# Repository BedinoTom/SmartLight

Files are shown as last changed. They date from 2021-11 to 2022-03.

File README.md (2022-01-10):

# SmartLight
Un boitier permettant de réguler l'éclairage publique, plus un dirigeable assurant la redondance du système.
## Cahier des charges
Le cahier des charges du projet : [Link](CdC.pdf)
## Rapport de séances
Un lien vers les rapports de séance : [Link](RapportSeance/Tom)
## Boitiers
Ce dossier contient tout le travail liée au boitier : [Link](Boitiers/README.md)
## Dirigeable
Ce dossier contient tout le travail lié au Dirigeable : [Link](Dirigeable/README.md)
## Images
Ce dossier contient toutes les images du projet : [Link](Images)
## Presentations
Ce dossier contient les divers présentations du projet : [Link](Presentations/README.md)

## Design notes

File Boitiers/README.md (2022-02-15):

# Boitier
Cette partie du git est réservé aux documents de développement du boitier.

## Programme
Voici la liste des progammes conçu pour le dirigeable:
- [Main](main_firmware) : Programme principale du projet.
- [Capteur Doppler](doppler_test) : Programme permettant de détecter un mouvement par effet Doppler.
- [Capteur Photodiode](lumen_test) : Programme permettant de lire le signal analogique 
représentant la quantité de lumière.
- [Timer](timer_test) : Programme permettant de sauvegarder et de lire la date.
- [Camera Thermique](temperatureMatrix) : Programme permettant de récuperer la matrice thermique.
- [Module bluetooth](ble_test) : Programme permettant de tester le bluetooth.
- [SmartApp](SmartLightApp) : Application Android.
- [c_lib](c_lib) : Fonctionnalitées pour décoder.
- [Bluetooth decode](ble_decode) : Programme de décodage des commandes de l'application

## Modèle 3D
Voici la liste des modèles 3D liée au boitier :
- [Plaquette](schema_impression_3d) : Modèle de la plaquette tenant les capteurs afin de les tester
en condition stable.

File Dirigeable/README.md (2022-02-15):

# Dirigeable
Cette partie du git est réservé aux documents de développement du dirigeable.

## Maixduino
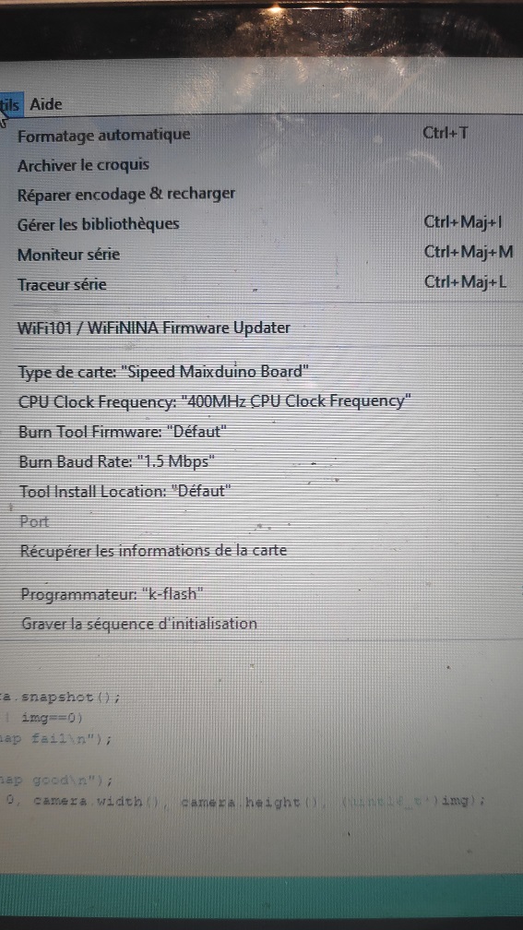
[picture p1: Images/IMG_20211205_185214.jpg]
Configuration
Voici une photo montrant la configuration IDE Arduino : 
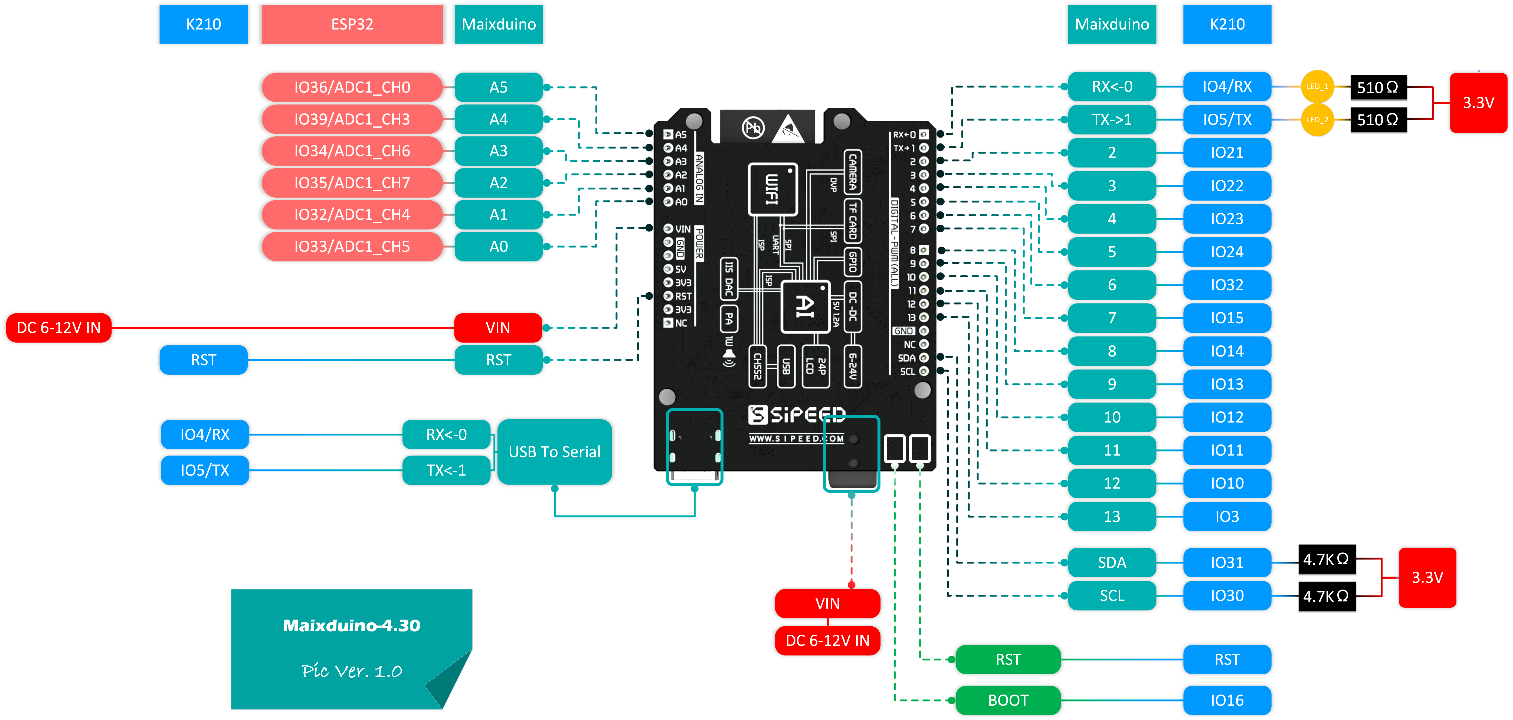
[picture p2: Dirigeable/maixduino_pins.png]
Pins Configuration
Voici la configuration des pins : 

## Programme
Voici la liste des progammes conçu pour le dirigeable:
- [Selfie](programme/selfie) : Programme permettant d'afficher le flux video de la camera sur l'écran.
- [main_firmware](programme/main_firmware) : Programme permettant d'effectuer la reconnaisse IA depuis la camera.
(Nécessite le modelè [m.kmodel](mobilenet_model/m.kmodel), il doit etre renomer en "m" et mis sur une SD) (OBSOLETE)
- [yolo_firmware](programme/yolo_firmware) : Programme permettant d'effectuer la reconnaisse IA depuis la camera.
(Le modèle [YOLO](yolo2_model/) est directement intégré dans le micrologiciel)
- [Controle_du_drone](controle_drone_firmware) : Programme pour controller les moteurs du drones.
- [arduino_i2c_slave](arduino_i2c_slave) : Programme I2C esclave.
- [ble_decode](ble_decode) : Programme de décodage des commandes bluetooth.
- [i2c_com](i2c_com) : Programme de la Maixduino pour communication "binaire".

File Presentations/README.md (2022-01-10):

# Présentations
Le projet d'Arduino qui nous a été confié cette année, nécéssite deux présentations. Une a mis parcours
et une à la fin. Elles sont toutes les deux présentes ici.

## Semestre 3
Voici celle réalisée lors du semestre 3 : [Link](S3)

## Semestre 4
Voici celle réalisée lors du semestre 4 : [Link](S4)

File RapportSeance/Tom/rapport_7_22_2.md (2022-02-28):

# Rapport de séance 7 du 22/02

Lors de cette séance, j'ai procédé au montage final du boitier avec tous les capteurs et composants nécéssaire. J'ai également utilisé
le travail éffectué à la maison afin de décoder les commandes envoyers par l'application. Pour finir j'ai recu le matériel afin
d'effectuer la liaison entre lampadaire.

## Travail éffectué à la maison

### Boitier

Juste avant le départ en vacance, j'ai déssiné puis imprimer un boiter en bois afin de contenir l'ensemble du système au sol.
Ce dernier a également 2 percages afin de laisser le champ de la caméra thermique libre et pour que la lumiere rentre et soit captée
par la capteur de luminosité. (On pourra la voir dans les images des sections suivantes)

### Communication Maixduino et Arduino

Lors des vacances j'ai finalisé la communication entre la Maixduino et l'Arduino, celle ci s'effectue par cable comme décrit dans 
le rapport précédent. La liaison est à présent pleinenement opérationnel.

### Réparation de la librairie

Les divers fonctions permettant de décoder les commandes aux format key=value; sont remplacés par une seul fonction, qui prend
en entrée le chaine brut, et la clé désirée et renvoie la valeur. La fonction a été réécrite avec des standards d'Arduino afin
qu'elle ne présente plus de bugs.

## Montage Final

Le but principal de la séance était de monter tous les capteurs ensembles et de faire fonctionner le programme principal. Il a donc
fallu monter tous les capteurs sur 2 board par soucis d'accécibilité. Et il a fallu fusionner tous les programmes qui ont été testé.
Comme on peut le voir sur l'image, la plaquette qui supporte le doppler et la caméra thermique a été collés dans la boitier par soucis
de simpliciter.
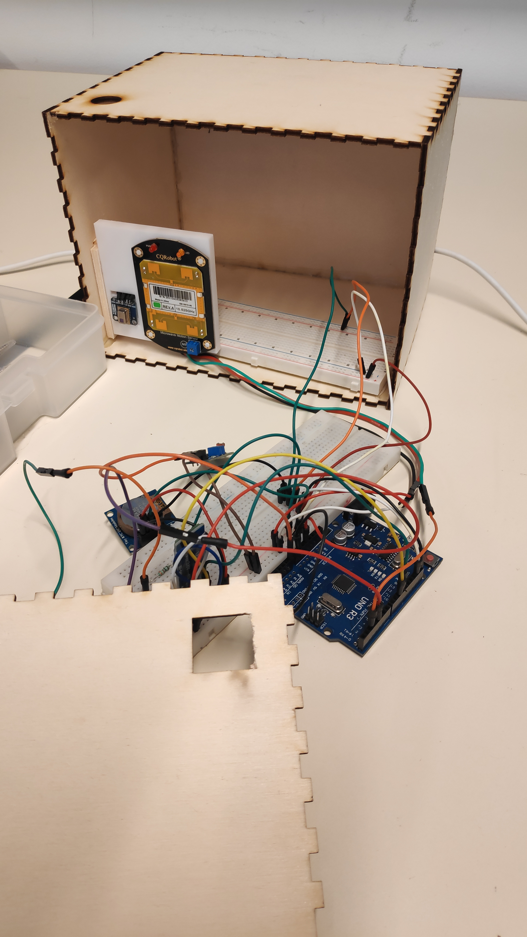
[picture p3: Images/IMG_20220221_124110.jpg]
Boitier

A la fin de la séance l'objectif était atteind, en effet je pouvais controller la détection à partir de l'application et les différents
moyens de détection fonctionnaient bien. Je pouvois voir en temps réelle sur l'application les différentes détections. Il existe un délais
de 4 secondes entre la détection et l'odre de fin de détection.
L'appliction recevait divers informations de l'Arduino.
Comme on peut le voir sur cette image.
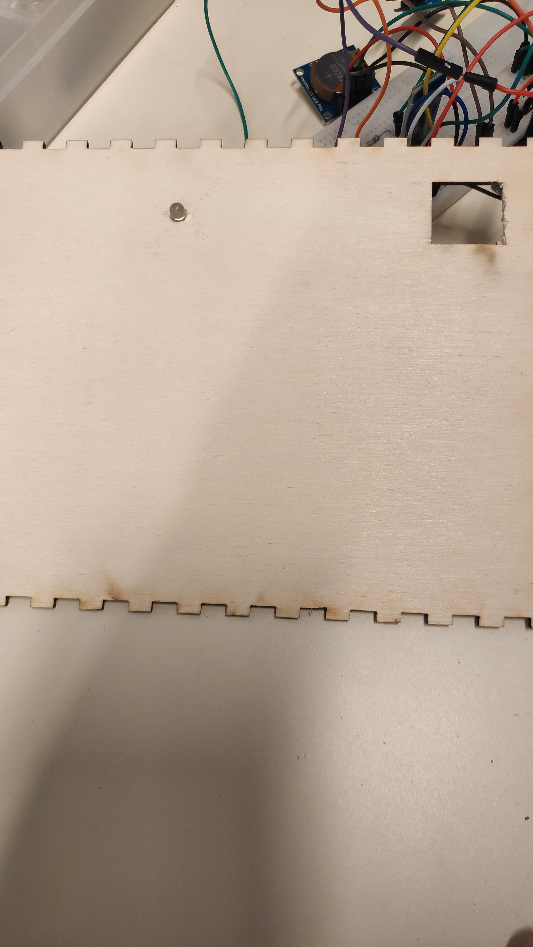
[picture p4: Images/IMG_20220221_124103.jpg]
LED

Un autre trou a été percé dans le boiter et une LED y a été fixée. Cette dernier joue le rôle de lampadaire. Elle est controllable par 
l'application. Elle sera pour la semaine prochaine controllé en fonction des détections.

## Liaison entre lampadaires

Enfin j'ai recu le matériel, comme le montre la photo, qui permettra de simuler la communication entre lampadaire.
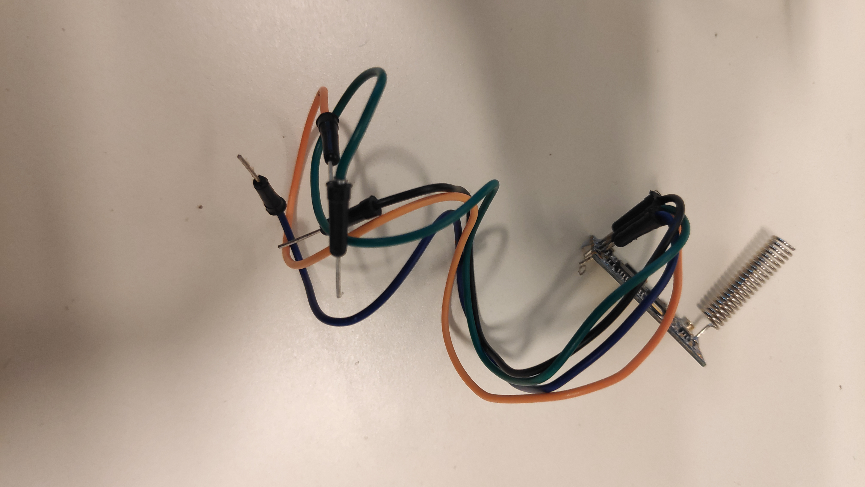
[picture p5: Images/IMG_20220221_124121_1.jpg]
Wireless

J'en possède plusiseurs qui vont simuler l'envoie et la réception d'ordre.
Un premier programme non fonctionnel a été crée [ici](../../Boitiers/wireless_com/wireless_com.ino).
Le but pour la prochaine fois est d'avoir cette liaison pleinement opérationnel.

## Travail à faire

Le travail suivant est à réaliser pour la prochaine fois :
- Liaison inter-lampadaire
- Module GPS et Compass pour le drone
- Liaison drone-lampadaire

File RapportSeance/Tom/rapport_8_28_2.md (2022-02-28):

# Rapport de séance 8 du 28/02

Lors de cette séance, j'ai finalisé le montage final du boitier. J'ai ajouté les modules de communication radio et le module GPS.

## Travail éffectué à la maison

En dehors des seances, j'ai commencé à faire marcher la liaison radion entre les lampadaires. Pour ce faire j'ai utilisé deux Arduino.
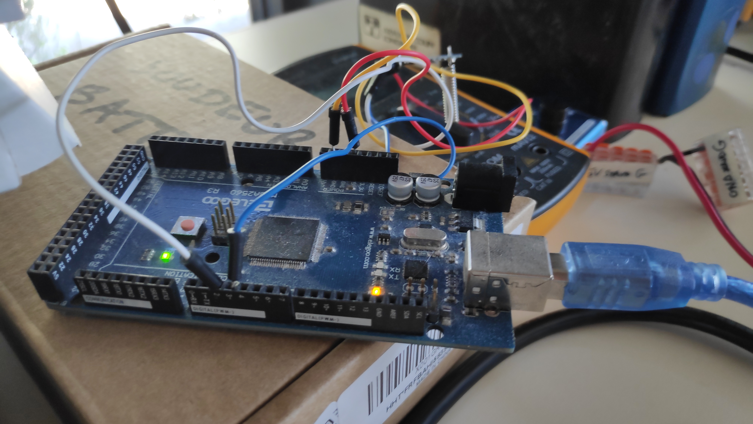
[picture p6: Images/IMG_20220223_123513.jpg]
Arduino 1

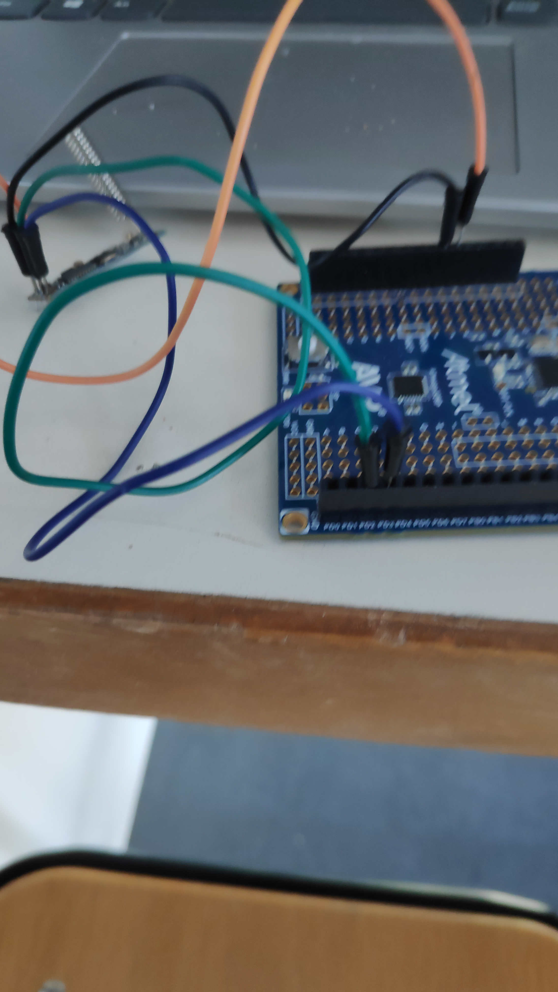
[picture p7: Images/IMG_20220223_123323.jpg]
Arduino 2

Chacune possédait le même programme [ici](../../Boitiers/wireless_com/wireless_com.ino). Ce dernier permet normalement d'envoyer et de
recevoir des données à travers le module.
Sauf que comme on peut le voire sur la capture les données ne vont que dans 1 sens.
Capture Ecran Capture d'écran

# Boitier

Lors de cette séance j'ai arrangé l'interieur de la boite afin qu'il n'y ai plus qu'une seul plaque et moins de câbles. J'ai égament percé
un trou afin de faire passer le câble pour l'alimentation. Comme on peut le voir sur l'image le boitier est entierement fermé et la lumière
est allumé par l'application bluetooth.
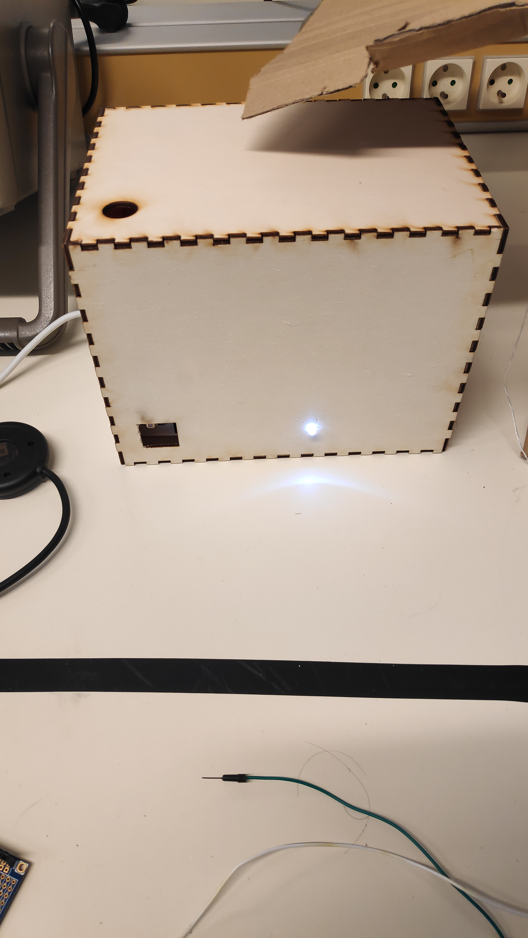
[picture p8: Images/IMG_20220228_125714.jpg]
Boitier

Sur la même application bluetooth on peut voir au niveau du RealTime qu'il est ON, cela veut dire qu'il a détecté un mouvement.
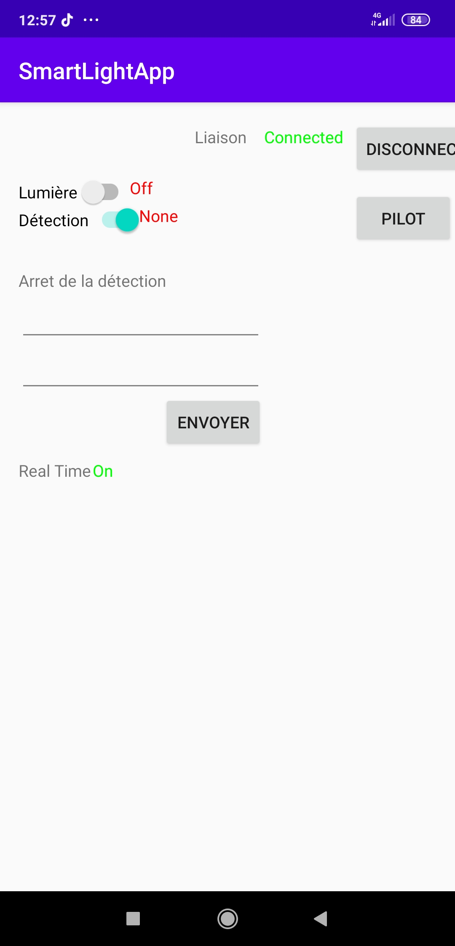
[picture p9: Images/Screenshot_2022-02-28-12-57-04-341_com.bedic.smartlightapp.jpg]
Application


# Module Radio

Lors de cette séance, j'ai essayé de résoudre les problèmes du module radio, mentionné plus haut. Malheuresement, apres des changements
de cartes, de câble et de soudure, le problème reste inchangé. Un module HC-12 sur les 3 dont je dispose répond aux commandes AT.
Il faut que je détermine si,cela a un rapport avec mon problème.

# GPS

Le Compass qui est en liaison I2C refuse de ce calibrer ce qui pose problème pour le dirigeable. De même le GPS pose
des soucis de liaisons sérials. Il ne la détecte plus. Je n'ai pas eu le temps de vérifier les câbles. (Les test sur 
les modules radio ont pris beaucoup de temps).

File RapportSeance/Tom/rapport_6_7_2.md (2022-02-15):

# Rapport de séance 6 du 07/02
Lors de cette séance, j'ai testé la nouvelle application Android, mis en marche les moteurs du dirigeable et relier par connexion filiaire
la Maixduino et l'Arduino Uno.

## Application Android

L'application Android a été mis à jours afin de répondre aux éxigence de commande du dirigeable. Pour cela une nouvelle page a été rajouté. Cette
dernière contient les boutons de commandes pour avancer, reculer, tourner à gauche, tourner à droite ou grimper. Il y a un boutton permettant
de stopper tous les moteurs. Tous ces dispositifs ne peuvent être activés que si le slide armement est allumé afin de s'assurer qu'il n'y
ai pas de pression parasite.
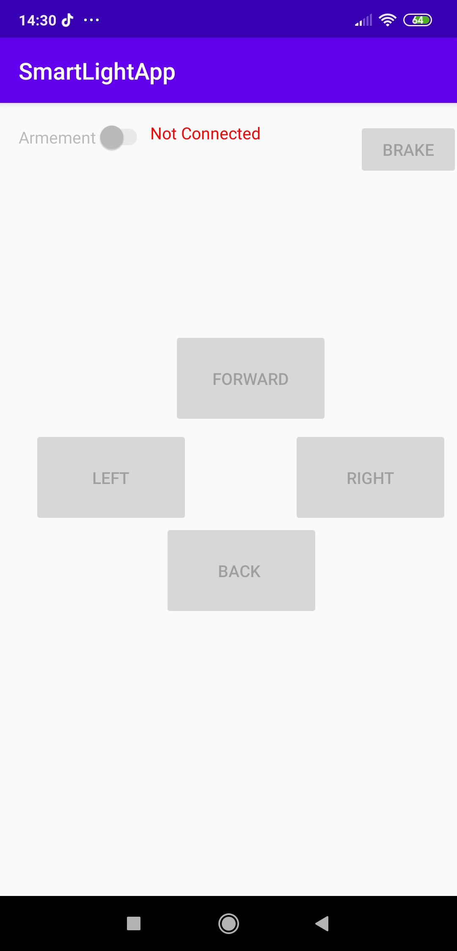
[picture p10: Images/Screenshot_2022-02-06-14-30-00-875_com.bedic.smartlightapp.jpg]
Prototyte d'application Prototyte de l'application
Voici la photo : 

## Boitier, moteurs et bluetooth

Pour cette séance l'objectif était que les moteurs puissent démarrer par eux-mêmes. Après avoir essayer un premier circuit d'alimentation
qui renvoyait du 5V après transformation d'une pile de 9V, les moteurs ne démarraient toujours pas par eux-même. Il a donc fallu brancher
directement la pile de 9V sur les moteurs afin que ces derniers démarrent par eux-mêmes.
Afin de décoder les ordres de l'application, j'ai voulu utiliser la librairie énoncée dans le rapport précédent. Sauf que l'Arduino rencontrait
des erreurs de mémoires, après test à part, il en vient que le programme utilise peut-être un modèle mémoire ordinateur. Mais comme les
commandes dans ce cas sont simples, j'ai opté pour un simple comparaison. Le problème de la librairie sera réglé plus tards.
Voici un lien vers les différents codes: [ici](../../Dirigeable/README.md) 
Voici également des photos et vidéos du dirigeable en fonctionnement ainsi que l'intérieur de la boite:
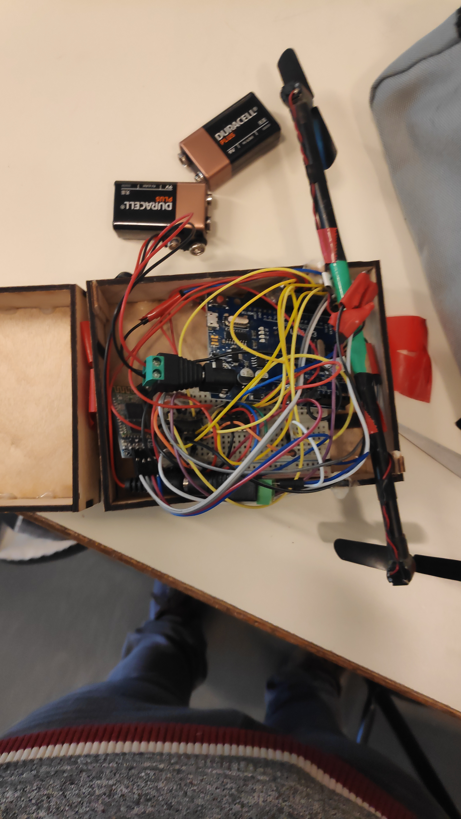
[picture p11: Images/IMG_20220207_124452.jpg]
Boitier interne

Video 1 Moteurs en action
Video 2 Moteurs en action

## Communication interne au dirigeable

Dans cette séance j'ai également posé les bases afin que la Maixduino la carte qui va servir à détecter les humains par vision et la carte
Arduino qui va communiquer par bluetooth à l'application.
Dans un premier temps une communication Serial a été envisagé mais difficile à mettre en place parce que la programmation se faisant
sur python la configuration des pins est très compliquées.
Ensuite un communication de type I2C a été envisagé, mais impossible à mettre en place car la Maixduino scan seulement certains périphériques
I2C sont reconnus.
Donc la derniere solution envisagée est la communication "binaire", c'est à dire qu'un premier fils est chargé de transmettre les requêtes
à la Maixduino et l'autre est chargé d'envoyer la réponse.
Le protocole qui doit être établir est le suivant : le fils 1 passe à 5V quand l'Arduino demande à la Maixduino si il y a quelqu'un
au bout de 5 secondes on lit la réponse sur le fils 2, si il est à 5V alors il y a quelqu'un.
La configuration des ports est compliqué car MaixPy support plusieurs cartes, donc à chaque début de programme, il faut indiquer les ports
utiliser et les nommers comme on peut le voir dans ce fichier : [ici](../../Dirigeable/i2c_com/i2c_com.py)
Et voici une image :
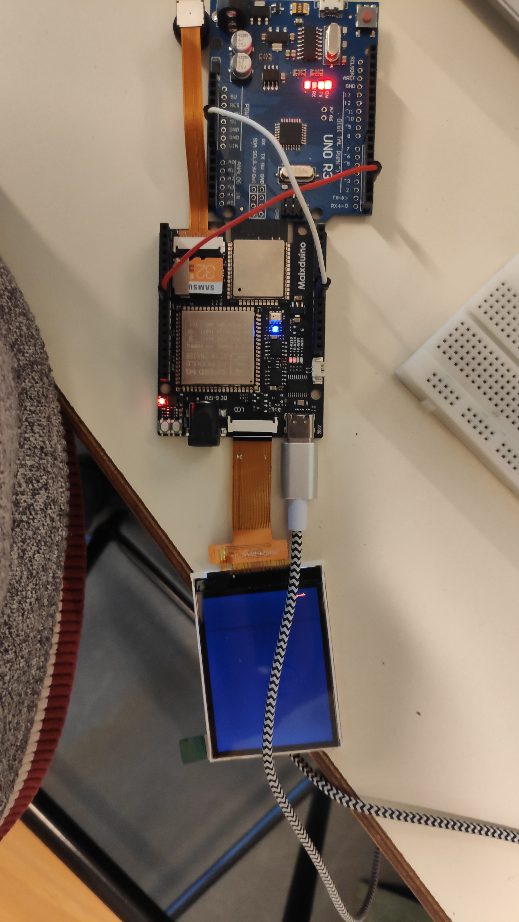
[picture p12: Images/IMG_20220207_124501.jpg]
Communication


## Travail à réaliser à la maison

A la maison il faut que j'effectue les tâches : 
- Réparer la librairie interne
- Mise au point de la communication entre Arduino
- Coder completement le système du boitier au sol (mise en commun de tous les bouts)
- Dessiner les plans pour la boite au sol

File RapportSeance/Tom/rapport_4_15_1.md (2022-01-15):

# Rapport de séance 4 du 15/01
Lors de cette séance, je suis passé à l'oral sur mon projet, j'ai également régler le problème
du capteur Doppler afin qu'il détecte correctement les mouvements. J'ai corrigé le problème 
d'alimentaion du module Timer. Pour finir j'ai ajouté le module de détection de la lumoière.

## Plaquette 3D
J'ai déssiné et imprimer une pièce en 3D qui permet de fixer les capteurs pour qu'ils ne bougent pas
et ne soit pas parasiter.

## Présentation
J'ai passè la première heure de la séance à reconstruire l'entièreté du système composé de
la reconnaissance par IA, du capteur thermique, du module Bluetooth et du Timer.
Puis j'ai relancé la liaison Bluetooth avec l'application.
Enfin j'ai présenté l'avancement de mon projet avec les différents capteurs, qui sont montés
sur une impression 3D que j'ai réalisé et quip permet de stabiliser les capteurs de mouvements
et de chaleur.

## Capteur Doppler
Monter le capteur Doppler sur la plaquette 3D, à parmis de le stabiliser, ce qui permet de ne
plus avoir de mouvements parasite. Le potentiometre permettant de gérer la distance a été
tourné vers le plus bas, puis remonter doucement afin d'atteindre une distance de détection
convenable. Il a ensuite été relié à l'Arduino afin de pouvoir envoyer une message Bluetooth
au portable.

## Camera Thermique
La camera thermique a été montée aussi sur la plaquette afin de stabiliser sa détection.

## Module Timer
Après mesure de tension, je me suis rendu compte que la pile du Timer n'envoyait qu'une tension
de 1,6V ce qui est trop peu pour que le module de sauvegarde de l'heure marche. Je l'ai donc
remplacé par une autre pile de 3V, ce qui a permis de le faire fonctionner correctement.
Il a pu retenir l'heure, même si l'Arduino était débranchée.

## Module Lumière
J'ai branché le module de lumière afin de détecter le luminosité ambiante pour déclencher où 
non les lampadaires.

## Dirigeable
Enfin, Monsieur Masson, m'a proposé de re-commander un dirigeable au près d'une entreprise espagnol.

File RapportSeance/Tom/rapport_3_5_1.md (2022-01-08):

# Rapport de séance 3 du 05/01
Lors de cette séance j'ai pu tester en condition réelle, la reconnaissance par IA. 
J'ai également fait réparer le module permettant de récupérer l'heure. J'ai aussi tester
le module bluetooth. J'ai ensuite utiliser le capteur thermique pour détecter le passage
d'une personne. Enfin j'ai commencer la calibration du radar doppler.
Voici le lien vers les codes: [link](../../Boitiers/README.md)

## Reconnaissance IA

Grâce au travail effectuer lors des vacances, la maixduino, reconnait maintenant les objects 
et les humains comme on peut le voir sur l'image ci-après:
Reconnaissance humains
On voit un premier plan un camarade qui est reconnu en tant que "person" ainsi que deux autres
dans le fond à gauche.
Afin de réaliser cela le langage de programmation a été changé nous sommes passé du C-Object à python.
En effet il existe une version du firmware (le micrologiciel qui gère la maixduino) qui accepte le
"live-python", c'est à dire que nous codons en python dans un ide et nous pouvons l'envoyer sur l'arduino
et voir le retour de l'ecran LCD sur le logiciel.
Comme on peut le voir ci-dessous (dans le cadre marquer "Pas d'image")
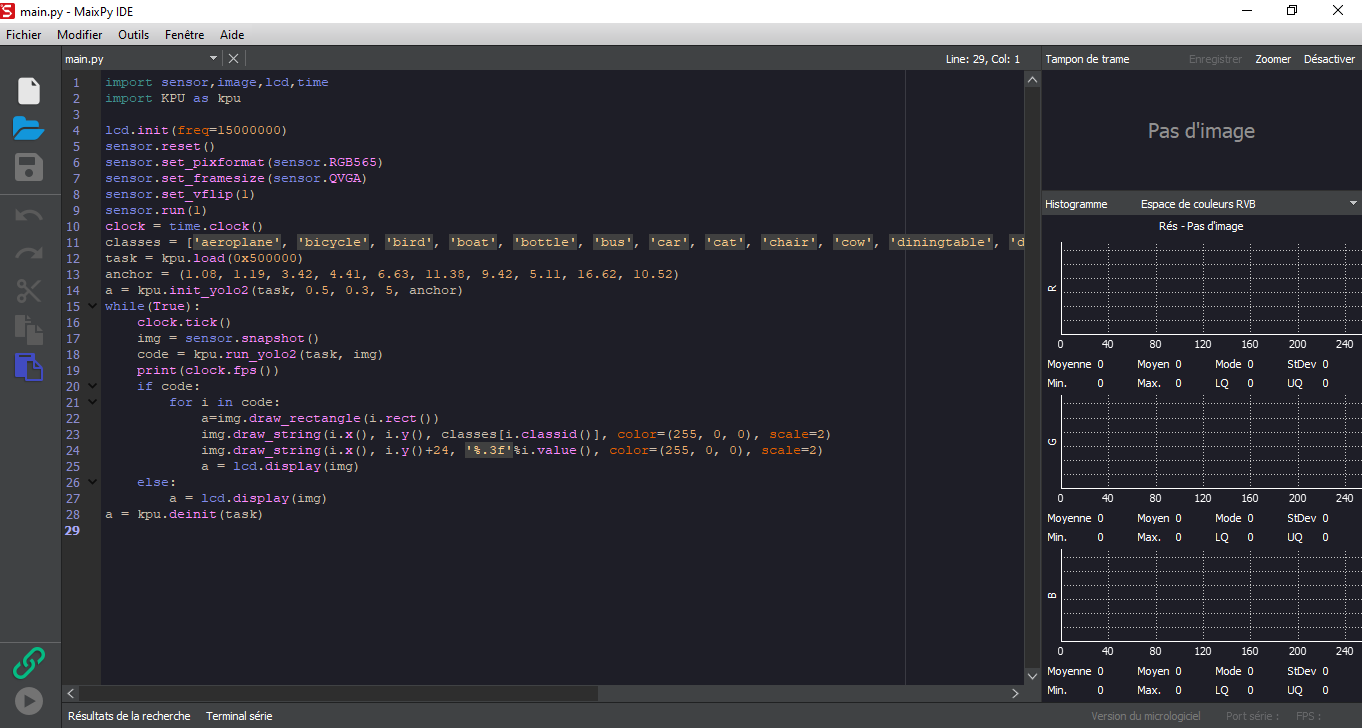
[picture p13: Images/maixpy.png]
Maixpy

Quand le programme fut finaliser, on peut l'inscrire dans le firmware, ainsi que le fichier
qui sert de modèle à l'IA, comme cela le code python le charge à partir d'une adresse 
mémoire, ce qui est plus rapide.

## Module Timer

Lors d'une nouvelle tentative afin de faire fonctionner le module permettant de retenir la date et l'heure
en mémoire, le module c'est trouvé être défectueux, il lui manquais une soudure permettant son alimentation
par la pile lorsque l'Arduino est éteinte. Après un nouveau test la date et l'heure ne sont toujours pas retenu.
On peut donc supposer un problème de pile. Je testerai chez moi avec une nouvelle pile.

## Module Bluetooth

Dans l'optique de pouvoir savoir si une personne passe devant un capteur sans devoir être devant l'écran de
l'ordinateur, ainsi que pouvoir commander l'exctinction et l'allumage j'ai voulu teste le module bluetooth,
ainsi que l'application sur portable. Après mise sous tension et programmation j'ai reussi à faire envoyer
un message du portable à l'arduino, ainsi que inversement.

## Camera Thermique 

J'ai voulu commencer à entrer dans le vif su sujet, et la détection des personnes. Pour cela j'ai combiner
le programme du timer, du bluetooth et de la caméra thermique. Cette derniere pointe sur son environnement.
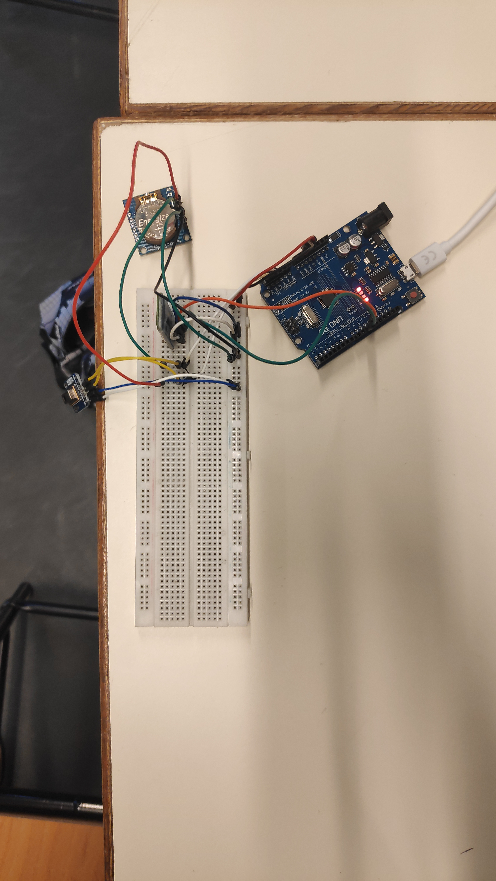
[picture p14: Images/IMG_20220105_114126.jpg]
Environnement

L'algorithme analyse la différence de température globale entre deux prises. Et au dessus d'un certain seuil
il envoie un message à travers le bluetooth au portable en disant qu'il y a une personne.
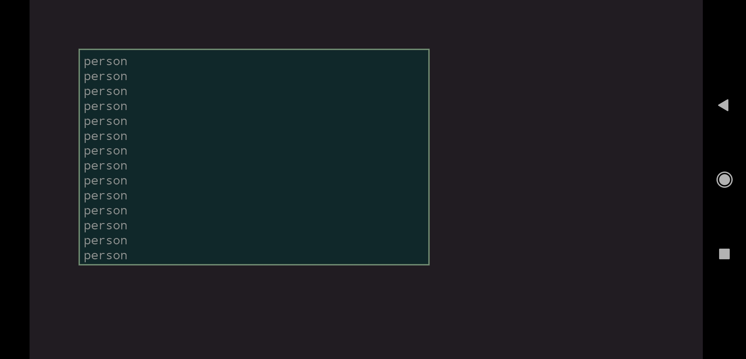
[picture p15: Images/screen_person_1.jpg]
Screen

Cette technique sera combinée avec le Doppler afin d'affiner la détection.

## Radar Doppler

Enfin, le Doppler a également été sorti afin de la calibrer et de le tester en environnement réel.
Il s'avère qu'il est compliqué au départ de comprendre qu'est ce qui dans la salle le fait clignoter.
Le programme ou la communication Arduino-PC plante aussi de temps en temps rendant compliqué la compréhension.
L'objectif suivant est donc de baisser la porter du radar avec un tournevis (sur le potentiomètre) avant de petit
à petit la monter afin de maitriser la zone de détection.

## Boitier

Objectif pour la semaine prochaine avoir un schema/plan du boitier qui va contenir le dispositif.

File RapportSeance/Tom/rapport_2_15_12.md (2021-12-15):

# Rapport de séance 2 du 15/12
Lors de cette séance j'ai testé les composants électroniques liés au boitier, essayer de comprendre
pourquoi l'IA ne fonctionnait pas et obtenu des précisions sur le matériel lié au dirigeable.
Voici le lien vers les codes des différents tests : [link](../../Boitiers/README.md)

## Travail de la séance

L'objectif de la séance était de vérifier que les composants marchaient, et de trouver le code
permettant de les faire fonctionner dans le cadre du projet.

### Module Doppler

Le premier module que j'ai testé est celui permettant la détection des personnes et véhicules
grâce à l'envoie d'une onde. Ce module possède 3 fils, 2 pour l'alimentation et 1 qui s'active
quand du mouvement est détecté. Après deux tests avec un simple programme lisant si le câble était
à LOW ou HIGH, puis un programme lisant le voltage du signal, je me suis rendu compte que le module
envoyait un signal très faible. M.Masson est intervenu en me disant que le module nécéssitait un
amplificateur pour être opérationnel. J'ai donc utilisé un autre module qui est déja équipé d'un
amplificateur opérationnel et qui possède la même configuration de câble que l'autre module.
Cette fois-ci un code d'exemple, a parfaitement marché, il ne restera plus que la calibration
de distance.

### Module Photodiode

Le second module que j'ai testé est celui permettant de capter la luminosité ambiante. Il est utilisé
pour que les lampadaires ne s'allument pas si la luminosité ambiante est deja assez élevée. Il est 
composé de 4 pins, 2 d'alimentations, 2 de données (1 qui renvoie une signal HIGH si la luminosité
dépasse un seuil controllable par un potentiomètre et 1 qui renvoie un signal analogique proportionnel
à la luminosité. Après un court programme exemple trouvé, et un test en mettant ma main sur le capteur
ce-dernier répondait bien au variation de lumière. Il ne reste plus qu'à trouver un formule pour 
convertir le signal analogique en lumens, l'unité de mesure de la lumière.

### Camera Thermique

Le troisième module que j'ai testé est celui permettant de détecter les personnes et les véhicules
par la chaleur. Ce module renvoie une matrice de température de 64 "pixels", il faut les analyser
et le mettre en corrélation pour détecter un chargement. Ce module est fonctionnel, il faut trouver
comment mettre en place la corrélation.

### Module Timer

Le dernier module que j'ai testé est celui permettant de garder en mémoire l'heure et la date courante.
Il est utilisé en complément du module de photodiode, en permettant l'activation ou la désactivation du
scanner par photodiode à des heures précises (par exemple pour des événements ou des travaux). Apres avoir
trouvé et testé le code d'exemple j'ai reussi à mettre le module à une certaine heure et la lire. En revanche
je n'ai pas reussi à conserver l'heure des que l'Arduino n'était plus alimenté. Cela est probalement du à
un soucis de pile que je devrait résoudre. La communication par le protocole I2C n'a pas été compliqué grâce
à la documention sur Internet.

### Correction IA

Lors de cette séance un des objectif était également de finir la reconnaissance de personnes et de véhicules 
par IA. En effet lors de la dernier séance par manque de temps cela avait était impossible. Après avoir
téléverser le code, l'écran reste indéfiniment sur le chargement. Afin de comprendre les problèmes une led verte
 et une led rouge ont été ajouter elle était sensé s'allumer en fonction de l'avancement et des erreurs.
 La communication Serial n'était pas disponible car j'effectuais les tests sur une autre Arduino en même temps
 et l'ordinateur ne pouvait supporter la charge de courant.
 Les résultasts ont montré que le chargement du modèle de prédiction s'effectuer correctement ainsi que 
 la détection mais que l'affichage rencontré un problème. Il devra être corriger.

### Dirigeable

Lors de la séance M.Masson m'a également montré, le dirigrable utilisé par les années précédentes afin que 
je vois comment je dois m'organiser. Le dirigeable est composé du ballon, et d'une nacelle équipée en
matériels de réception d'ordre et d'une télécommande. Tout cela sera étudié dans les derniers séances. Le dirigeable
 est considéré comme un apport esthétique, la plus value étant sur l'IA.

## Travail à faire

Pour la prochaine séance le travail à faire à la maison est :
- Corriger et terminer l'IA
- Corriger le Timer
- Trouver la formule pour la photodiode
- Calibrer le Doppler 
- Mettre en place la corrélation de la camera thermique

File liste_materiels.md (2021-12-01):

# Liste du matériels

1. magnétomètre
2. gps
3. maixduino
4. capteur luminosité
5. radar doppler
6. lora
7. ble
8. timer 

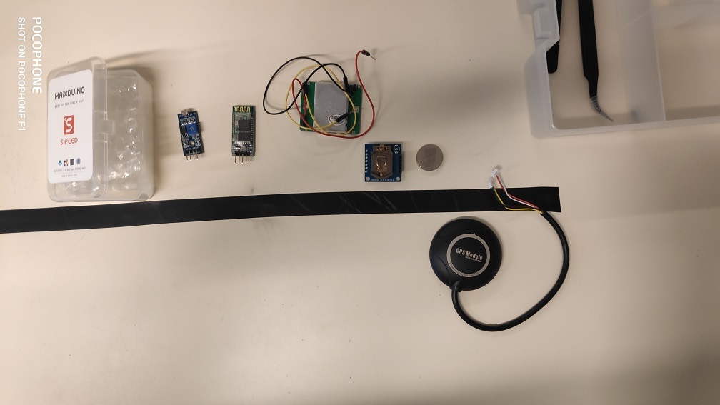
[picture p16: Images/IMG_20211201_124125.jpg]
Matériels


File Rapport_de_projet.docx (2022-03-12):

# Rapport de projet

Tom Bedino PEIP2 G3

Sommaire

# I. Etat final du projet & Comparaison

Commençons par un rapide extrait du cahier des charges montrant de la description du projet.

« Le projet SmartLight a pour but de concevoir un système autonome, léger et économique permettant de réguler l’allumage et l’extinction de l’éclairage publique. Ce système doit pouvoir détecter de personnes et des véhicules passant dans son champ et allumer l’éclairage public en conséquent, en respectant les contraintes de sécurité liées au code de la route. Pour cela le système principal comprend un boîtier se fixant aux différents lampadaires, le système secondaire lui comprend un dirigeable équipé d’une caméra qui permet d’éteindre des lampadaires qui ne se seraient pas éteints avec le système principal. »

Pour pourvoir effectuer une comparaison avec l’état actuel du projet, il faut également entrer plus dans les détails des différents points techniques qui étaient initialement visés. Pour cela nous reprenons une version simplifiée du tableau des fonctions.

Légende :

Noir = boîtier

Rouge = dirigeable

Fonctions | Expression | Critères d’appréciations
Principale 1 | Allumer éteindre les luminaires en fonction du passage d’individus ou de véhicules Éteindre les lampadaires qui ne se seraient pas éteins eux-mêmes | Distance minium de 15 mètres autour du lampadaire Détection minium d’un humain Allumage à des horaires corrects Repérer par IA des humains et des véhicules
Contrainte 1 | Le luminaire doit résister à un grand nombre de cycles d’allumage Doit pouvoir repérer des points lumineux | Au minimum le système doit supporter un grand nombre d’allumage/extinction Repérer une source lumineuse qui correspond à un lampadaire
Contrainte 2 | Le système doit pouvoir s’adapter à la puissance fournie Doit fonctionner sur batterie | Avoir au minimum une solution pour gérer toutes les puissances possibles
Contrainte 3 | Le système doit être compact afin de pouvoir se greffer sur les luminaires | -Boîtier en forme de carré
Contrainte 4 | Le système doit être hermétique afin de protéger les passants du risque électrique Le dirigeable doit être télécommandable. | -Matériaux isolants

Les fonctions liées au prix, à la résistance et à l’esthétique ont été retirées car elles n’ont pas été traitées par manque de temps.

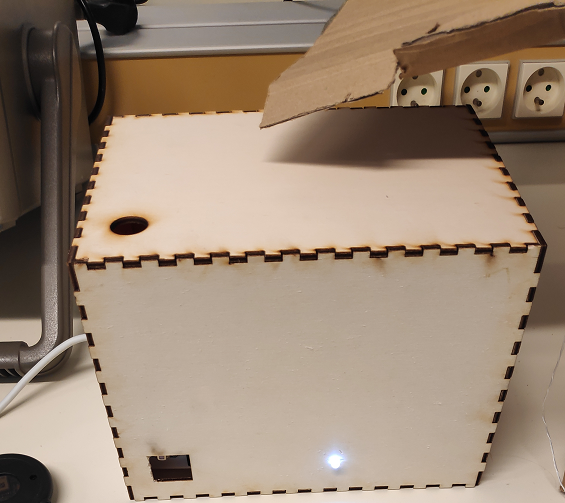
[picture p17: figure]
Boitier en fonctionnement.

Figure 1 : Boitier en fonctionnement

Comme on peut le voir ici, l’aspect physique du boitier est terminé. Dans cette photo le boitier est en fonctionnement et me détecte ce qui provoque l’allumage de la LED. Cette dernière est là pour simuler un lampadaire qui s’allume.

Le principe de détection est géré par une caméra thermique et un module radar, qui se charge respectivement de voir des mouvements de chaleurs ou de matières. On voit d’ailleurs la caméra thermique à travers le trou carré de la boite.

Le trou rond sert à faire passer la lumière afin que le boitier puisse savoir s’il fait jour ou nuit.

Pour ce qui est de la sécurité, ici la boite en bois est fermée ce qui empêche toutes interactions est donc risque d’électrocution.

Les seules fonctions qui n’ont pas été implémentées sont celles de l’allumage et l’extinction selon l’heure, même si le module de gestion du temps est à l’intérieur. Cependant il n’est pas inutile, en effet il sert à compter les secondes avant que le lampadaire ne s’éteigne.

Enfin la communication avec les autres lampadaires est faite par radio. Puis le Bluetooth sert à la gestion interne du lampadaire.

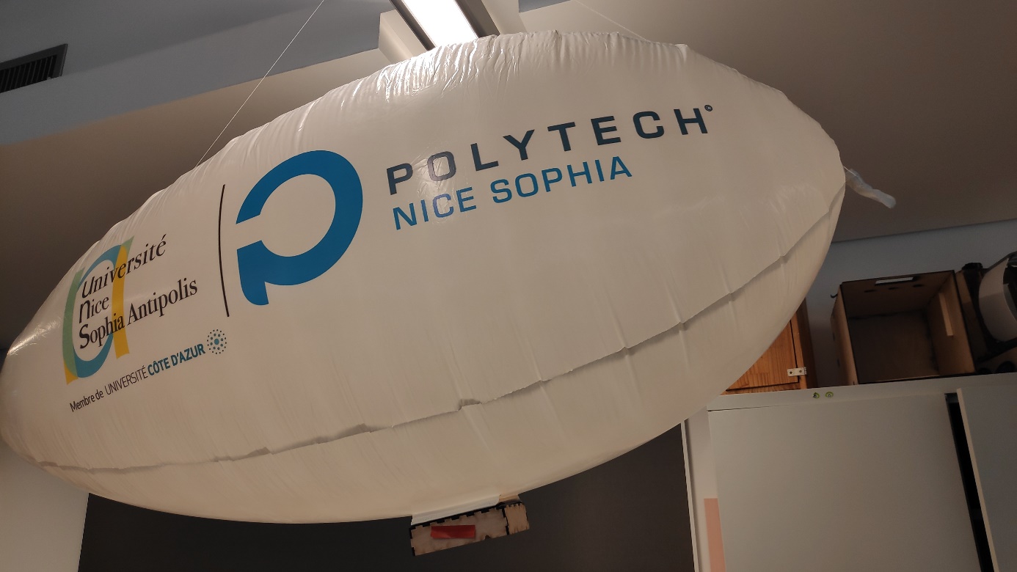
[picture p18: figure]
Dirigeable en vol

Figure 2 : Dirigeable

Pour ce qui est de la partie dirigeable, seules les fonctionnalités de détection par IA et de motorisation non-autonome ont été réalisées. En effet, le dirigeable présent sur la photo, contient de l’air et non de l’hélium, il ne peut pas voler de plus il possède des trous. Donc les fonctionnalités de communication et pilotage automatique ont été abandonnées au profit des autres parties.

Pour continuer nous allons montrer les deux algorithmes liés au boiter et au dirigeable.

Algorithme du boitier :

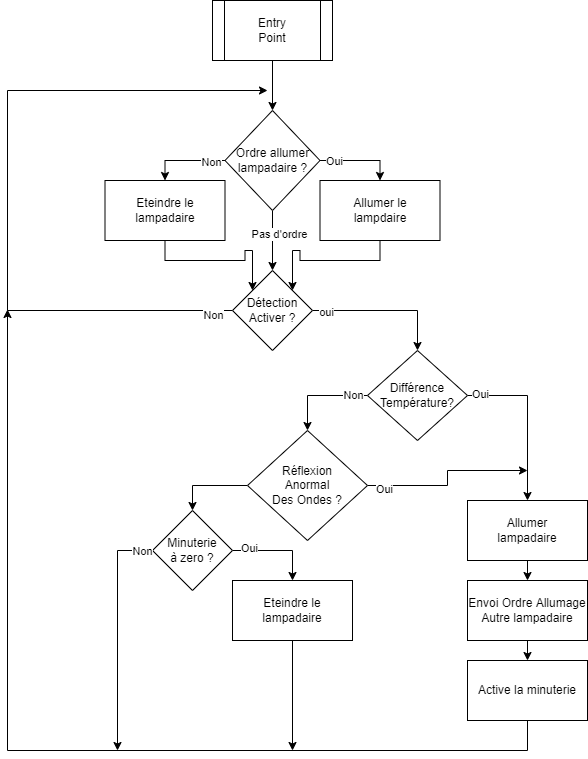
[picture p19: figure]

Algorithme du dirigeable :

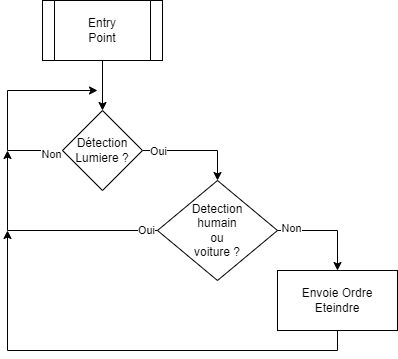
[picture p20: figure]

Enfin pour finir voici le planning du projet telle qu’il s’est passé, en comparaison avec celui prévu :

Figure 3 : Diagramme de Gantt Rétro

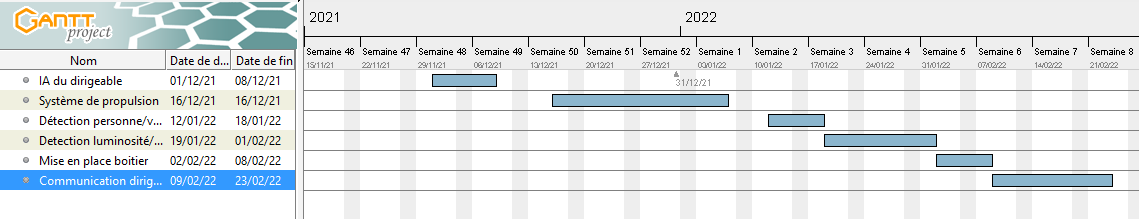
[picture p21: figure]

Figure 4 : Diagramme de Gantt Prévisionnel

On peut voir que la tâche de communication du dirigeable a été supprimée, et que celle liée à la détection du boitier a été considérablement allongé.

# II. Développement & Problèmes

Dans cette partie nous allons voir les différentes phases de développement du projet, avec le lot de difficultés qu’elles ont apporté.

Commençons par la phase contenant l’intelligence artificielle. Ici, le but est d’avoir un système capable de détecter des humains et des voitures. Pour cela il a été utilisé un maixduino Arduino capable de faire de l’IA. Ce n’est pas une carte standard Arduino donc la compatibilité avec IDE Arduino a posé de nombreux problèmes. En effet, les exemples proposés étaient limités, certains ne fonctionnaient pas, et de plus le site du constructeur est en chinois, avec une version traduite anglais mais pour du python. D’où par la suite le passage sous python pour la programmation, plus précisément, sous micro-python, une version adaptée aux microcontrôleurs.

Cependant d’autres problèmes sont apparus quand il a fallu utiliser un ficher modèle pour l’IA. Le « tuto » du site en anglais indiqué qu’il lisait le modèle depuis une adresse mémoire. Il m’a ensuite fallu comprendre comment mettre ce ficher dans l’adresse mémoire.

Pour finir quand il a fallu relier la maixduino et l’Arduino Uno afin d’envoyer des ordres au Bluetooth, il s’est posé un problème de pin. En micro-python il faut définir nous même la configuration des pins et leurs numéros.

Passons maintenant à la phase de développement de la motorisation du dirigeable. Pour cette phase la programmation n’a pas été compliquée car le programme avait déjà été réalisé en cours, et les branchements étaient déjà fait. Le problème est venu de l’alimentation qui a été sous dimensionner. Il a fallu chercher plusieurs solutions et faire des mesures afin de voir quelle était la meilleure façon de procéder. Finalement deux piles de 9V ont été retenues, une pour l’Arduino et une autre pour les moteurs.

Continuons avec la phase de développement des détecteurs de mouvements. L’utilisation de la caméras thermiques et du module doppler n’ont posé quasiment aucun problème hormis celui pour calibrer les capteurs. En effet la caméra thermique permet de calculer la différence de température entre deux instants. Celle-ci n’est jamais égale à zéro il a fallu trouver un compromis. De même pour le doppler, il a fallu trouver une valeur de sensibilité cohérente.

Pour la phase de communication, le module Bluetooth a été très facile à mettre en place et à configurer. En revanche le module Radio 433 Mhz a été plus compliqué à mettre en place, non pas à cause de ces branchements qui sont les mêmes que le Bluetooth mais à cause d’une erreur lors de la phase de test. En effet 2 modules ont été testé, l’un sur une Arduino UNO comme dans le boiter, l’autre sur une Arduino Méga jouant le rôle d’un autre lampadaire. Le problème est venu que le module était branche sur de mauvais pin pour l’Arduino Méga simulant alors une panne des modules qui n’existaient pas. Le problème a été détecté et corrigé en 1 séance.

Enfin pour finir, étudions la phase de mise en commun des modules. Des problèmes sont apparus quant à la réception des commandes permettant de donner des ordres à l’Arduino. Après recherche, de mauvaises fonctions étaient utilisées. Ensuite un problème avec la fonction millis est apparue, cette dernière ne renvoyait pas le bon temps, c’est la que le module TImer est entré en jeu. Il aura fallu deux séances pour corriger ces problèmes.

# III. Retour sur expérience

Après avoir fait ce projet et acquis de l’expérience, je pense que si je devais refaire ce projet je compartimenterais plus les deux réalisations, c’est-à-dire que je me concentrerais uniquement sur le boiter puis sur le dirigeable ou inversement. Ici je pense qu’un des problèmes a été le passage à quelques reprises du boitier au dirigeable et inversement, qui a dû

faire perdre du temps, car à chaque fois il fallait relire tout ce qui avait été fait.

Je pense aussi que si je devais le refaire, cela se fera en équipe, une autre personne pourrait m’aider en faisant le dirigeable pendant que je ferais le boitier est inversement.

Enfin si je possédais quelques semaines de plus, il faudrait tester le boiter en condition réel, car la caméra thermique détectant les variations de température, il y a un risque qu’elle soit leurrée par le vent. Ensuite il faut voir la porte du module doppler. Enfin évidement il faut mettre au point le déplacement autonome du dirigeable et sa communication avec les lampadaires.

# IV. Bibliographie

Sipeed Maixduino : https://maixduino.sipeed.com/en/

Arduino Documentation : https://docs.arduino.cc/

Camera Thermique : https://projetsdiy.fr/test-camera-thermique-amg8833-amg8831-avec-du-code-arduino-capteur-infrarouge-matriciel-64-points/

Module Doppler:

http:/cqrobot.wiki/index.php/10.525GHz_Doppler_Effect_Microwave_Motion_Sensor_SKU:_CQRSENWB01

Moteur, Bluetooth, Analog Input : http://users.polytech.unice.fr/~pmasson/Enseignement-arduino.htm

HC-12 : https://www.aranacorp.com/fr/utilisation-dun-module-hc-12-avec-arduino/

Rapport de Projet Smart Light Bedino Tom

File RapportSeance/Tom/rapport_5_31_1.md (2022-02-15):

# Rapport de séance 5 du 31/01
Lors de cette séance j'ai testé l'application Android et la librairie C faites à la maison. Avec Monsieur Masson, nous avons gonflé
et accroché l'ancien dirigeable afin que je puisse effectuer des tests avec lui. J'ai mis en marche les moteurs et commencé à travailler
le GPS.

## Application Android

La semaine dernière, j'ai mis au point un application Android afin de communiquer avec le module Bluetooth. L'application donnée lors
du cours ne suffisait plus. Cette dernière peut se connecter au module Bluetooth et lui envoyer divers commandes complexes au format
clé=valeur;clé2=valeur2;. L'application sert à activer/désactiver le lampadaire, activer/désactiver le processus de détection.
L'application peut envoyer une date et une heure pour désactiver la détection. Et pour finir elle peut savoir si une personne ou
un véhicule a été détecté.
Voici une capture d'écran:
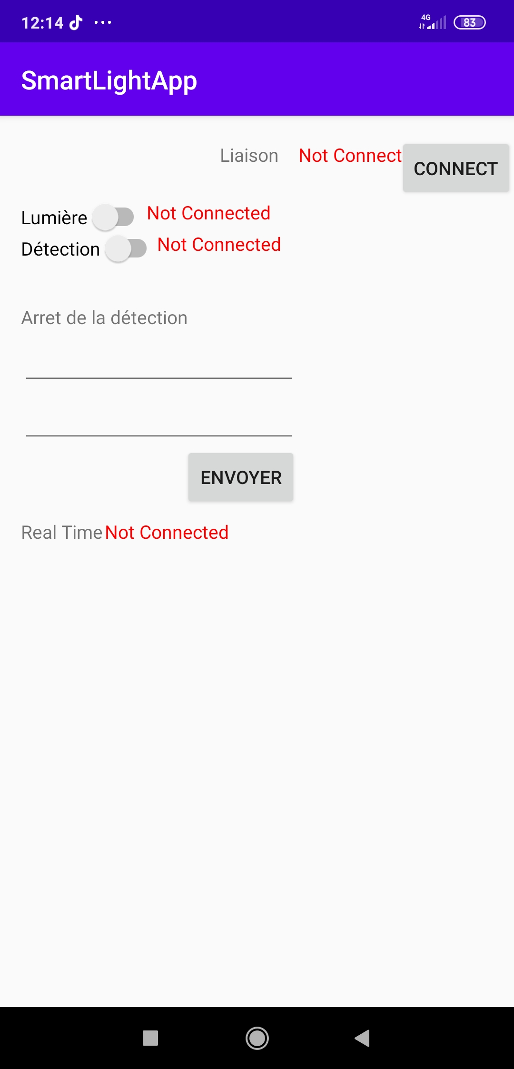
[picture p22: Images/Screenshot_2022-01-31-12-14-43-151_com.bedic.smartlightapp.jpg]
Prototyte d'application Prototyte de l'application

L'application sera enrichie prochainement afin de pouvoir controller le dirigeable.

## Librairie C

La semaine dernière, j'ai également mis au point des fonctions en C afin de pouvoir décoder les commandes complexes envoyées par
l'application. Ces dernière doivent être manipulées avec précaution car elle alloue de la mémoire donc en cas d'erreur, elles
peuvent corrompre la mémoire de la carte.
Voici le lien de la librairie avec un exemple : [ici](../../Boitiers/c_lib/split_lib.c)

## Dirigeable

Lors de cette séance, M.Masson et moi-même avons sorti le dirigeable de son carton. Il possédait de nombreuses déchirures.
Après les avoir réparer, M.Masson a gonflé le ballon jusqu'à qu'il prenne forme puis la accroché dans la salle, comme le montre
l'image ci-dessous. Ce dirigeable est temporaire, en attendant le nouveau.
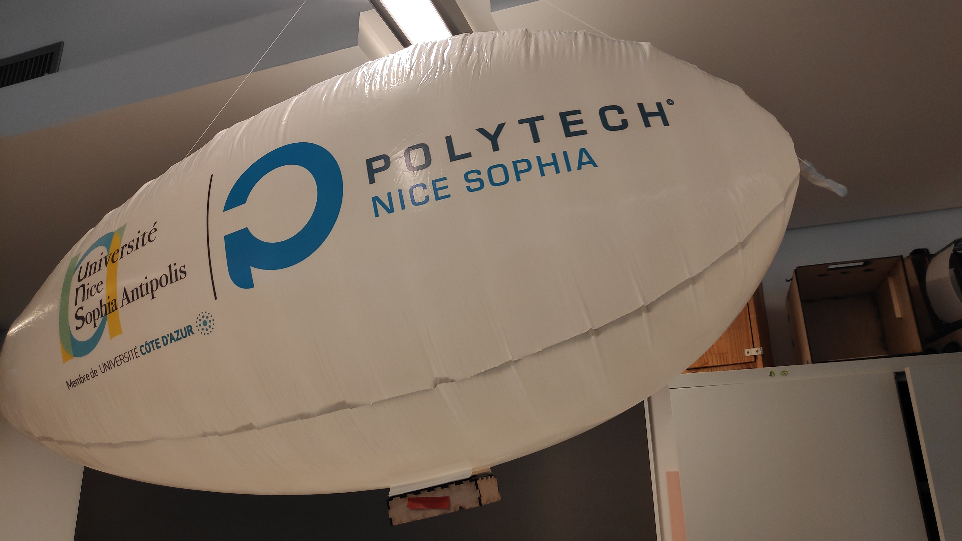
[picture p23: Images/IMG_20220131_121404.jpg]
Dirigeable

Comme ce dernier est accroché, il n'y a pas de contrainte de poids.

### Boitier et moteurs

Ensuite j'ai aussi récupéré le boitier permettant de controller les 3 moteurs : 2 pour avancer et 1 pour monter. Nous pouvons
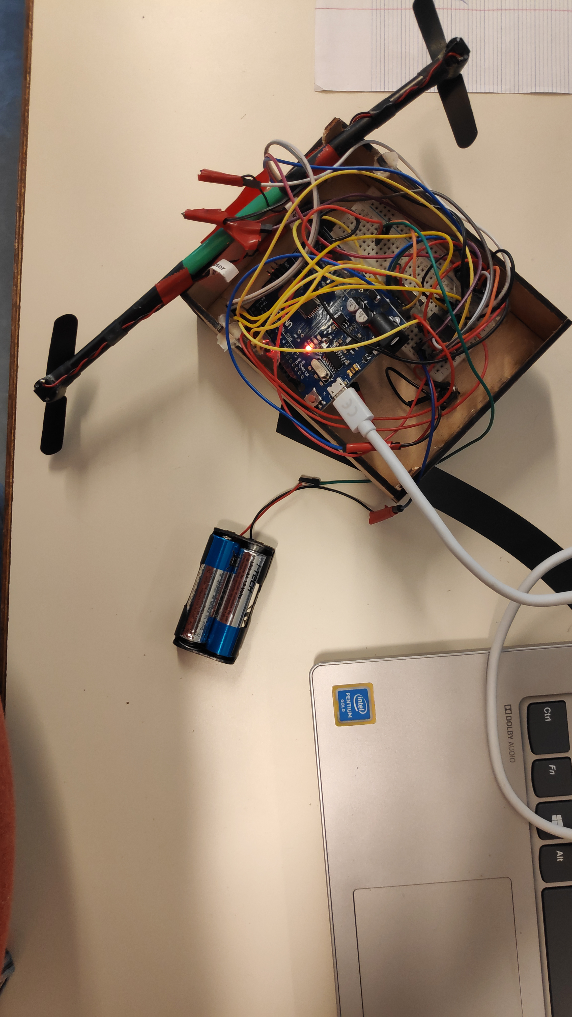
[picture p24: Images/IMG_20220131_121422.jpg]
Moteur
le voir sur l'image ci-contre : 
Les moteurs sont controllés par l'Arduino qui va recevoir ses ordres d'un module Bluetooth (ce dernier a été configuré).
Le programme de test des moteurs est fait (disponible [ici](../../Dirigeable/controle_drone_firmware/controle_drone_firmware.ino))
Il y a eu un problème d'alimentation avec les moteurs, en effet ces derniers tirés leurs énergies de la carte qui ne leurs
donnait que 400 millivolt. Je suis donc passé sur une alimentation par pile de 3V mais qui n'est toujours pas suffisante. Il faudra
tester une autre alimentation de 5V.

### GPS

Pour que le dirigeable puisse être piloté, il lui faut le module GPS. Grâce à l'image suivante et à M.Masson j'ai pu avoir
le câblage et la librairie TinyGPS++ qui me permet de récuperer les codes d'exemples. Lors du premier test, à l'extérieur
aucun signal n'a été reçu, il faudra réssayer.
Cablage

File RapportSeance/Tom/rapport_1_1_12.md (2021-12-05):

# Rapport de séance 1 du 01/12
Lors de cette séance, j'ai recu le matériel lié au projet.
La liste de ce matériel est disponible [ici](../../liste_materiels.md)

## Travail à la maison
Avant de commencer le rapport de la séance je vais rapporter ici le travail effectuer à la maison avant la première séance
Dans le but de concevoir un dirigeable capable de voler gràce à des ballons d'helium, un premier prototype a été construit.
Il était constitué de ballons remplis d'helium attachés à une arduino. Divers problèmes ont été rencontrés :
- les premiers ballon gonflés n'ont atteint que environ 60% de leurs volumes maximum.
> Problème réglé en les gonflant plus longtemps.
- les premiers serrages de ballon étaient insuffisant, l'helium s'échappait trop rapidement.
> Problème réglé en modifiant le serrage.
- il fallut plusieurs essaies de ficelle pour trouver la plus fine, la plus lègère et la plus résistante.
- il fallut trouver la bonne configuration pour l'équilibrage
- un problème c'est posé sur le temps de vol, d'après l'expérience les ballons n'ont volés que quelques heures.
> Problème non résolu.

Protyte de dirigeable

## Travail de la séance

L'objectif de la séance était de réaliser la détection des personnes et véhicules par l'IA.

### Réalisation de la détection

Après avoir récuperer l'Arduino spécial IA que je nommerais la Maixduino. J'ai commencé par configuré l'IDE Arduino
afin qu'il reconnaisse cette nouvelle carte. Je suis ensuite allé chercher le code d'exemple permettant d'effectuer la reconnaissance
sur le site suivant [link](https://github.com/sipeed/Maixduino/tree/master/libraries/Maix_KPU/examples/mobilenet_v1).
Dans le même temps j'ai téléchargé le modèle(le fichier qui dit comment faire la reconnaissance) sur une carte SD que j'ai ensuite
inséré dans la Maixduino. J'ai ensuite branché l'écran LCD qui devait faire le retour vidéo.
> Problème : la Maixduino nécéssite une connectique USB-C que je n'avais pas.
Afin de ne pas rester coincé et de perdre du temps je suis passé sur la compréhension du module GPS qui sera détaillé
dans la section suivante.

Après avoir recu le cable j'ai téléversé le programme.
> Problème : aucun téléversement.

Les recherches ont montrés que le problème venait d'une erreur de configuration de l'IDE rapidement réglé.
> Problème : l'écran LCD était noir et le moniteur serie indiquais un message d'erreur.

Pour l'écran l'erreur venait d'une mauvais branchement sans conséquence pour le matériel. Pour le message d'erreur du moniteur série,
cela a été plus compliqué. Il a fallu analyser le code. Ce-dernier montrais que la caméra utilisée était une OVH2460 or celle 
fourni avec la Maixduino est une GC0328. Il a donc fallu téléchargé une librairie approprié (facilité par le récurrence
de ce problème sur le github de la Maixduino) et modifié le code de l'exemple afin de remplacer le nom de la camére.
Après ces problèmes résolus, le programme a démarré comme montre l'image suivante :
Maixduino
Je n'ai pas d'image du fonctionnement de l'IA car le modèle est long à charger et qu'à cause du soucis de USB-C, il était
la fin du temps imparti. Des précisions seront apportées dans le prochain rapport.

Voici un lien vers les codes : [link](../../Dirigeable/README.md)

### Compréhension du GPS

Dans l'attente de l'USB-C, je me suis penché sur un autre aspect du dirigeable qui est le pilotage GPS. Pour cela j'ai
obtenu un module GPS qui contenait également un compass (circuit permettant d'obtenir la direction magnétique).
GPS/Compass
> Problème : le modèle possède six câbles sans aucune indication.

Des recherches ont été effectués, et on permis de montrer que les 4 câbles permettait d'alimenter les modules et d'avoir
une liaison série avec le module GPS et les 2 câbles permettait d'avoir une liaison I2C avec le module compass.
Cela a permis d'alimenter une premier fois le module afin de voir s'il fonctionnait. Les recherches ont aussi permis de trouver la librairie
pour le compass, son modèle est HMC5883L, et le [site](https://electroniqueamateur.blogspot.com/2019/06/fabrication-dune-boussole-avec-le.html) suivant indique un code pour le tester.
En ce qui concerne le module GPS, sa liaison série envoie les données en permanence, il reste à trouver une librairie pour les décoder.

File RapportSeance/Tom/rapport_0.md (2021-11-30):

# Rapport de pré-séance
Ce rapport de pré-séance fait le 30/11 est la ppur indiquer que le cahier des charges ainsi que le diagramme de Gantt ont été effectué.
Les deux sont disponilbes dans le GitHub. Ils ont été fait en accords avec les cours de sciences de l'ingénieur que j'ai effectué en Terminal.
Ils contiennent une description du besoin, la réponse technique et son fonctionnement.
Par ailleurs des début de recherche ont été entrepris à la maison, ils seront notifiés dans le rapport 1.

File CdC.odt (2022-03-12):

Cahier des Charges

Projet SmartLight

Bedino Tom

2021–2022

Polytech Nice Sophia

I. Description générale

Le projet SmartLight a pour but de concevoir un système autonome, léger et économique permettant de réguler l’allumage et l’extinction de l’éclairage publique. Ce système doit pouvoir détecter de personnes et des véhicules passant dans son champ et allumer l’éclairage public en conséquent, en respectant les contraintes de sécurité liées au code de la route. Pour cela le système principal comprend un boîtier se fixant aux différents lampadaires, le système secondaire lui comprend un dirigeable équipé d’une caméra qui permet d’éteindre des lampadaires qui ne se seraient pas éteints avec le système principal.

II. Partie Fonctionnelle


Dans cette partie nous allons exprimer les besoins auxquels le système doit répondre et comment il y répond.

Le diagramme suivant montre la fonction principale ainsi que les fonctions de contraintes qui vont s’imposer au projet.


Le tableau suivant reprend le diagramme ci-dessus en détaillent précisément la fonction avec les divers critères de réussite qui lui sont accordés et les écarts tolérés.

Noir = boîtier

Rouge = dirigeable

Fonctions | Expression | Critères d’appréciations | Niveau de flexibilité
Principale 1 | Allumer éteindre les luminaires en fonction du passage d’individus ou de véhicules Éteindre les lampadaires qui ne se seraient pas éteins eux-mêmes | Distance minium de 15 mètres autour du lampadaire Détection minium d’un humain Allumage à des horaires corrects Repérer par IA des humains et des véhicules
Contrainte 1 | Le luminaire doit résister à un grand nombre de cycles d’allumage Doit pouvoir repérer des points lumineux | Au minimum le système doit supporter un grand nombre d’allumage/extinction Repérer une source lumineuse qui correspond à un lampadaire | Meilleur cas : système à puissance variable Pire cas : système binaire
Contrainte 2 | Le système doit pouvoir s’adapter à la puissance fournie Doit fonctionner sur batterie | Avoir au minimum une solution pour gérer toutes les puissances possibles
Contrainte 3 | Le système doit être compact afin de pouvoir se greffer sur les luminaires | -Boîtier en forme de carré
Contrainte 4 | Le système doit être hermétique afin de protéger les passants du risque électrique Le dirigeable doit être télécommandable. | -Matériaux isolants
Contrainte 5 | Le système doit être protégé contre les agressions extérieures | -Boîtier solide résistance à des chocs légers -IP 14 minimum
Contrainte 6 | Le système doit avoir un coût relativement faible afin de pouvoir être déployé massivement
Contrainte 7 | Le système doit être esthétiquement acceptable | Doit avoir un couleur variable pour être le plus discret possible

Le dirigeable possède peut de fonctions de contrainte car ces dernières sont plus difficile à réaliser en un temps raisonnable.

III. Partie Structurelle

Dans cette partie nous allons exposer la structure du système avec les problèmes techniques qui se posent et les réponses qui lui sont apportées.

Nous commençons par la structure du système principale qui est le boîtier

Allumage

Et

Extinction

Luminaires

Relais électromagnétique

Détection de la lumière environnante

Détection

Personne/Véhicule

Réception/Envoie

Ordre

Allumage/Extinction

Capteur de luminosité

Capteur de mouvement

Capteur de chaleur

Carte micro-onde

RF 433MHz ou Lora 865MHz

Nous poursuivons avec la structure du dirigeable.

GPS / magnétomètre Moteur Ballons d’helium Carte RF 433 Mhz ou Lora 865 MHz

Éteindre

Lampadaire qui ne devrait pas être allumé

Détecter

humain/véhicule

Pourvoir se diriger

Et se repérer

Pouvoir

bouger

Pouvoir

flotter

Envoyer/Recevoir

Des ordres

Camera

Arduino IA

Ensuite nous allons voir comment l’information et l’énergie sont utilisées dans les deux systèmes.

Boîtiers :


Dirigeable :


II.Partie Comportementale

Dans cette dernière partie nous allons voir le comportement des systèmes dans leur environnement de travail avec un détails des différentes actions menée.

Comportement boîtier :

Début

Test si Personne/ vehicule Envoie ordre Allumage Luminaire autour Allumer luminaire Luminosité faible Ordre entrant

oui

non

oui

non

oui

non

Exécuter

ordre

Début Lumière forte Prise d’image à la caméra Traitement image Envoie Ordre exctinction Vérification Humain/Véhicule Comportemental dirigeable :

Mouvement vers le prochain point GPS

oui

non

non

oui

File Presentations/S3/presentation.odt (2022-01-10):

Présentation S3

Bonjours à tous, je vais vous faire la présentation de mon projet d’Arduino, qui se nomme SmartLight. Ce-dernier est un projet visant à créer un module permettant dé réguler l’éclairage publique, afin d’effectuer des économies d’électricité et de réduire la pollution lumineuse.

Pour cela le module se charge de détecte des personnes ou des véhicules afin d’allumer/ éteindre les lampadaires adéquats.

Ce projet comporte également un partie avec un dirigeable équipée d’une caméra. Il a pour but d’assurer la redondance du système en éteignant les lampadaires qui devraient être éteint (panne système, dysfonctionnement), pour cela il est équipé d’une IA qui reconnaît les personnes et les véhicules afin de connaître l’état dans lesquelles devrait être le lampadaire.

Jusqu’à maintenant j’ai réalisé la partie du dirigeable permettant de reconnaître par IA, les humains et les voitures. Pour cela j’utilise YOLO un modèle d’IA pré-entrainé permettant de reconnaître une multitude d’objet. J’ai juste besoin d’appliquer un filtre sur les résultats pour savoir ce qui a été détecté. Ensuite je n’aurais plus qu’à réaliser la partie permettant d’envoyer le message au lampadaire.

Pour ce qui est de la partie du boîtier qui s’accroche sur le lampadaire, j’ai déjà effectuer un montage avec la caméra thermique ainsi qu’une liaison Bluetooth. L’Arduino m’envoie un message « personne » lorsque une personne passe devant la caméra à cause d’un changement thermique. L’Arduino fait la différence entre deux instants des températures et à partir d’un certain seuil calculé, le message se déclenche.

J’ai également réalisé la plaquette imprimé en 3D qui permet de tenir les composants afin qu’ils soient stable.

J’ai également tester le module Doppler mais avec des difficultés car je ne connais pas précisément la distance de détection, ni le rayon car ce capteur peut détecter autour de lui.

Enfin le module de luminosité et celui qui se charge de l’heure sont opérationnelles, ils permettrons chacun de paramétrer quand est ce que la boîtier doit éteindre les lampadaires et commencer la recherche de personne et quand ils doit l’arrêter. Cela permet un flexibilité du système en cas de besoin (fête,accident, travaux).

Il me reste un travail sur toute la mise en place du dirigeable , la mise en commun de tout les modules et la communication entre boiter et dirigeable.

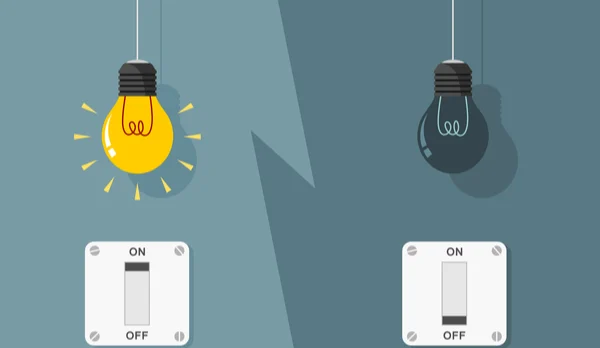
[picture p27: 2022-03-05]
Images/économie électricité maison ampoule allumée.webp

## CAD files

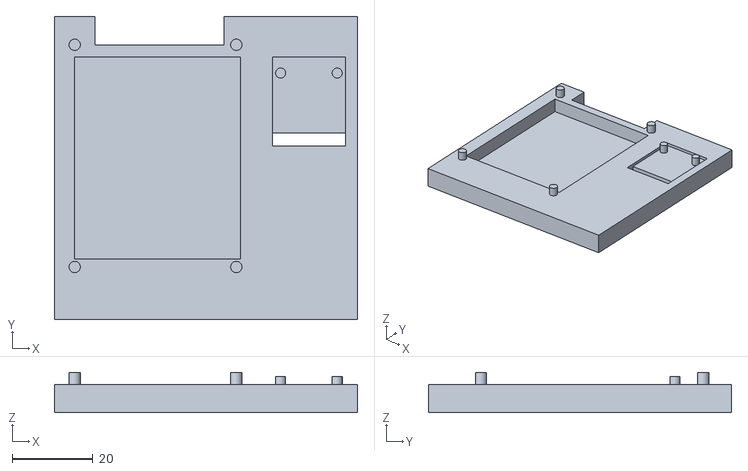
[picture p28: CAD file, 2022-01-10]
Boitiers/schema_impression_3d/prod_v2.stl
75.0 x 75.0 x 10.0

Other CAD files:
Boitiers/schema_impression_3d/plaque_support_capteur_v1.FCStd
Boitiers/schema_impression_3d/prod_v1.stl

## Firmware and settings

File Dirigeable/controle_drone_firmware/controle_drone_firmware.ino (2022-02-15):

#include <SoftwareSerial.h>

#define RX 3
#define TX 2

SoftwareSerial BlueT(RX,TX);
char buf[500];
int i=0,valid=0;

//Moteur
#define A 23
#define B 24
#define C 25
#define AVANT 26
#define ARRIERE 27
#define STOP 28

const int enable_A=10;
const int in_1_A=7;
const int in_2_A=6;

const int enable_B=9;
const int in_1_B=4;
const int in_2_B=5;

const int enable_C=11;
const int in_1_C=12;
const int in_2_C=13;

void setup() {
 Serial.begin(9600);
 delay(500);
 BlueT.begin(9600);
 delay(500);
pinMode(enable_A,OUTPUT);
pinMode(in_1_A,OUTPUT);
pinMode(in_2_A,OUTPUT);

pinMode(enable_B,OUTPUT);
pinMode(in_1_B,OUTPUT);
pinMode(in_2_B,OUTPUT);

pinMode(enable_C,OUTPUT);
pinMode(in_1_C,OUTPUT);
pinMode(in_2_C,OUTPUT);


}

void loop() {
while(BlueT.available())
  {
    if(i>=499)
     {
        break;
     }
     char c = char(BlueT.read());
     if(c == ';')
     {
      valid++;
     }
     buf[i] = c;
     i++;
  }

  if(valid == 1)
  {
    buf[i] = '\0';
    valid=0;
    i=0;

    if(strcmp(buf,"dir=brake;") == 0)
    {
      stop_all();
    }
    else if(strcmp(buf,"dir=up;") == 0)
    {
      delayMicroseconds(200);
      forward();
      power_all(255);
    }
    else if(strcmp(buf,"dir=down;") == 0)
    {
      delayMicroseconds(200);
      other_forward();
      power_all(255);
    }
    else if(strcmp(buf,"dir=left;") == 0)
    {
      delayMicroseconds(200);
      left();
      power_all(255);
    }
    else if(strcmp(buf,"dir=right;") == 0)
    {
      delayMicroseconds(200);
      right();
      power_all(255);
    }
    else if(strcmp(buf,"dir=climb;") == 0)
    {
      delay(200);
      climb();
      power_all(255);
    }

   sprintf(buf,"");
  }
}


void direction_motor(int n,int s)
{
  if(n==A)
  {
    if(s==AVANT)
    {
      digitalWrite(in_1_A,HIGH);
    digitalWrite(in_2_A,LOW);
    }
    else if(s==ARRIERE)
    {
      digitalWrite(in_2_A,HIGH);
  digitalWrite(in_1_A,LOW);
    }
    else
    {
      digitalWrite(in_2_A,LOW);
  digitalWrite(in_1_A,LOW);
    }
  }
  else if(n==C)
  {
    if(s==AVANT)
    {
      digitalWrite(in_1_C,HIGH);
    digitalWrite(in_2_C,LOW);
    }
    else if(s==ARRIERE)
    {
      digitalWrite(in_2_C,HIGH);
  digitalWrite(in_1_C,LOW);
    }
    else
    {
      digitalWrite(in_2_C,LOW);
  digitalWrite(in_1_C,LOW);
    }
  }
  else
  {
    if(s==AVANT)
    {
      digitalWrite(in_1_B,HIGH);
    digitalWrite(in_2_B,LOW);
    }
    else if(s==ARRIERE)
    {
      digitalWrite(in_2_B,HIGH);
  digitalWrite(in_1_B,LOW);
    }
    else
    {
       digitalWrite(in_2_B,LOW);
  digitalWrite(in_1_B,LOW);
    }
  }
}

void stop_all()
{
  direction_motor(A,STOP);
  direction_motor(B,STOP);
  direction_motor(C,STOP);
  power_all(0);
}

void forward()
{
  direction_motor(A,AVANT);
  direction_motor(B,AVANT);
  //direction_motor(C,AVANT);
}

void other_forward()
{
  direction_motor(A,ARRIERE);
  direction_motor(B,ARRIERE);
  //direction_motor(C,ARRIERE);
}

void left()
{
  direction_motor(A,AVANT);
  direction_motor(B,ARRIERE);
}

void right()
{
  direction_motor(A,ARRIERE);
  direction_motor(B,AVANT);
}

void climb()
{
  direction_motor(C,AVANT);
}

void power_motor(int n,int pwm)
{
  if(n==A)
  {
    analogWrite(enable_A,pwm);
  }
  else if(n==C)
  {
    analogWrite(enable_C,pwm);
  }
  else
  {
    analogWrite(enable_B,pwm);
  }
}

void power_all(int pwm)
{
  power_motor(A,pwm);
  power_motor(B,pwm);
  power_motor(C,pwm);
}

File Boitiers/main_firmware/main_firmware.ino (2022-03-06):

#include "Wire.h"
#include <Melopero_AMG8833.h>
#define DS1307_I2C_ADDRESS 0x68 // the I2C address of Tiny RTC
#include <SoftwareSerial.h>

#define RX 10
#define TX 11
#define RX_WIRELESS 7
#define TX_WIRELESS 8
#define LED_PIN 4
#define TIME_DETECT_STAY_ON 4

Melopero_AMG8833 sensor;
SoftwareSerial BlueT(RX,TX);
SoftwareSerial Wireless(RX_WIRELESS,TX_WIRELESS);
byte second, minute, hour, dayOfWeek, dayOfMonth, month, year;
float matrix_temp[64];
bool is_empty_matrice=true,is_collide=false,led_state=false,last_led_state=true,detect_state=false,last_detect_state=true, standby_collide=false;
int count_doppler=0,timer_doppler=0,timer_collide=0;
String buf;
int valid=0;

void getValueFromKeyMap(String _map, char* key, char*buf);

void setup() {
Wire.begin();
Serial.begin(9600);
BlueT.begin(9600);
Wireless.begin(9600);
//setDateDs1307(); //Set current time;
sensor.initI2C();
Serial.print("Resetting sensor ... ");  
int statusCode = sensor.resetFlagsAndSettings();
Serial.println(sensor.getErrorDescription(statusCode));

Serial.print("Setting FPS ... ");
statusCode = sensor.setFPSMode(FPS_MODE::FPS_10);
Serial.println(sensor.getErrorDescription(statusCode));

for(int i=0;i<8;i++)
{
  for(int j=0;j<8;j++)
  {
    matrix_temp[i + j*8] = 0.0f;
  }
}

attachInterrupt(digitalPinToInterrupt(2), stateChange_doppler, FALLING);
timer_doppler=millis(); 

pinMode(LED_PIN,OUTPUT);
digitalWrite(LED_PIN,HIGH);
}


void loop()
{
//delay(200);
getDateDs1307();//get the time data from tiny RTC

  //Serial.print("Updating thermistor temperature ... ");
  int statusCode = sensor.updateThermistorTemperature();
  //Serial.println(sensor.getErrorDescription(statusCode));

  //Serial.print("Updating pixel matrix ... ");
  statusCode = sensor.updatePixelMatrix();
  //Serial.println(sensor.getErrorDescription(statusCode));

  //Serial.print("Thermistor temp: ");
  //Serial.print(sensor.thermistorTemperature);
  //Serial.println("°C");

  //Serial.println("Temperature Matrix: ");
  float diff=0;
  if(!is_empty_matrice)
  {
    for (int x = 0; x < 8; x++){
      for (int y = 0; y < 8; y++){
        diff = diff + abs(sensor.pixelMatrix[y][x] - matrix_temp[y*8 + x]);
      }
    }
  }

 // Serial.print("Diff Temp : ");
  //Serial.println(diff);

  if(diff > 30)
  {
    is_collide=true;
  }

  for (int x = 0; x < 8; x++){
      for (int y = 0; y < 8; y++){
        matrix_temp[y*8 + x] = sensor.pixelMatrix[y][x];
      }
    }

  if(is_empty_matrice)
  {
    is_empty_matrice=false;
  }

  //Serial.print("Light : ");
  //Serial.println(analogRead(A0));

 if(((second+60*minute)-timer_doppler)>1)
  {
     if(count_doppler>1)  
     {
        is_collide=true;
        count_doppler=0;   //Count zero
    }
    else
    {
        count_doppler=0; 
    }
    timer_doppler=second+60*minute;
  }

  if(is_collide && detect_state && !standby_collide)
  {
    BlueT.println("collide=on;");
    Serial.println("COLLIDE");
    Wireless.println("collide");
    timer_collide=second+60*minute;
    digitalWrite(LED_PIN,LOW);
    is_collide=false;
    standby_collide=true;
  }
  
  if(((second+60*minute) - timer_collide)>TIME_DETECT_STAY_ON && standby_collide && detect_state)
  {
    Serial.println("OFF");
    BlueT.println("collide=off;");
    Wireless.println("collide");
    digitalWrite(LED_PIN,HIGH);
    standby_collide=false;
  }

  BlueT.listen();
  while(BlueT.available())
  {
    buf = BlueT.readString();
     valid++;
  }

  if(valid > 0)
  {
    Serial.println(buf);
    char values[50],arg1[50];
    getValueFromKeyMap(buf,"cmd",values);
    getValueFromKeyMap(buf,"arg1",arg1);
    Serial.println(arg1);
    if(strcmp(values,"light")==0)
    {
      if(strcmp(arg1,"true")==0)
      {
        led_state=true;
      }
      else
      {
        led_state=false;
      }
    }
    else if(strcmp(values,"detect")==0)
    {
      if(strcmp(arg1,"true")==0)
      {
        detect_state=true;
      }
      else
      {
        detect_state=false;
      }
    }
    valid=0;
  }

if(led_state != last_led_state)
{
  if(led_state)
  {
    digitalWrite(LED_PIN,LOW);
    BlueT.println("light=on;");
  }
  else
  {
    digitalWrite(LED_PIN,HIGH);
    BlueT.println("light=off;");
  }

  last_led_state = led_state;
}

if(detect_state != last_detect_state)
{
  if(detect_state)
  {
    BlueT.println("detect=on;");
  }
  else
  {
    Serial.println("ok");
    BlueT.println("detect=off;");
  }

  last_detect_state = detect_state;
}
}

void stateChange_doppler()  //Interrupt function
{  
  //Serial.println("State");
  count_doppler++;  
}


// Convert normal decimal numbers to binary coded decimal
byte decToBcd(byte val)
{
return ( (val/10*16) + (val%10) );
}
// Convert binary coded decimal to normal decimal numbers
byte bcdToDec(byte val)
{
return ( (val/16*10) + (val%16) );
}
// Function to set the currnt time, change the second&minute&hour to the right time
void setDateDs1307()
{

second =45;
minute = 16;
hour = 10;
dayOfWeek = 3;
dayOfMonth =5;
month =1;
year= 21;
Wire.beginTransmission(DS1307_I2C_ADDRESS);
Wire.write(decToBcd(0));
Wire.write(decToBcd(second)); // 0 to bit 7 starts the clock
Wire.write(decToBcd(minute));
Wire.write(decToBcd(hour)); // If you want 12 hour am/pm you need to set
// bit 6 (also need to change readDateDs1307)
Wire.write(decToBcd(dayOfWeek));
Wire.write(decToBcd(dayOfMonth));
Wire.write(decToBcd(month));
Wire.write(decToBcd(year));
Wire.endTransmission();
}
// Function to gets the date and time from the ds1307 and prints result
void getDateDs1307()
{
// Reset the register pointer
Wire.beginTransmission(DS1307_I2C_ADDRESS);
Wire.write(decToBcd(0));
Wire.endTransmission();
Wire.requestFrom(DS1307_I2C_ADDRESS, 7);
second = bcdToDec(Wire.read() & 0x7f);
minute = bcdToDec(Wire.read());
hour = bcdToDec(Wire.read() & 0x3f); // Need to change this if 12 hour am/pm
dayOfWeek = bcdToDec(Wire.read());
dayOfMonth = bcdToDec(Wire.read());
month = bcdToDec(Wire.read());
year = bcdToDec(Wire.read());
/*Serial.print("Date : ");
Serial.print(hour, DEC);
Serial.print(":");
Serial.print(minute, DEC);
Serial.print(":");
Serial.print(second, DEC);
Serial.print(" ");
Serial.print(month, DEC);
Serial.print("/");
Serial.print(dayOfMonth, DEC);
Serial.print("/");
Serial.print(year,DEC);
Serial.print(" ");
Serial.println();*/
//Serial.print("Day of week:");
}
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

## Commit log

2021-11-28 Cahier des charges
    Mise au point du cahier des charges.
2021-11-28 Diagramme de Gantt
    Mise en place du diagramme de répartition des tâches
2021-12-15 Seance 2 v1
    -Ajout du rapport de seance du 15/12
    -Ajout des programmes du boitiers
    -Ajout instructions de debug sur l'IA
2022-01-10 Home Work 1
    -Creation du modèle 3d pour soutenir les capteurs
    [plaque_support_capteur_v1.FCStd, prod_v1.stl]
2022-01-10 Home Work 1.2
    -Changement/Correction dans le modèle 3D
    [plaque_support_capteur_v1.FCStd, prod_v2.stl]
2022-01-20 Android app v0.1
    -Prototype Application android
2022-01-23 HomeWork 2
    -Ajout d'une lib pour décoder les commandes
2022-01-30 HomeWork 3
    -Sortie de la version 0.1 de l'application
2022-02-15 Adnroid app v0.2
    -Ajout de l'activité de pilotage du drone
2022-02-15 Homework 4
    - Fichier de base pour la communication
2022-02-21 HomeWork 5
    - Mise à jour de la librairie de décodage d'information
    -Finalisation de la communication Maixduino et Arduino
2022-02-21 Seance 7 v1
    -Montage Final
    -Wireless
2022-02-28 Seance 8 v1
    -Tentive résolution Wireless,GPS,Compass
